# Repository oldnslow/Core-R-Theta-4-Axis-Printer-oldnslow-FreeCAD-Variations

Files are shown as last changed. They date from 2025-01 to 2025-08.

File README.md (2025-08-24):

# The Core R-Theta Printer

This repository is intended to be a series of FreeCAD versions of jyjbird's 4 axis, polar, "core-RΘ" 3D printer – an entirely new type of multi axis 3D printer designed from the ground up. To start a FreeCAD version of the "original" (f8d197c circa 16 Mar 2025 commit) will be generated.  Check out the [Wiki](https://github.com/oldnslow/Core-R-Theta-4-Axis-Printer/wiki) for build guides, links to useful sites/videos and other hopefully useful information. 

Check out jyjbird's [youtube video](https://www.youtube.com/watch?v=VEgwnhLHy3g) to see it in action!
Watch the video (https://www.youtube.com/watch?v=VEgwnhLHy3g)

### Slicer
A multi axis printer is pretty hopeless without a non-planar slicer, which is why I built this quick [radial slicer](https://github.com/jyjblrd/Radial_Non_Planar_Slicer) for the printer. This leverages the printer's rotating nozzle to print simple parts without supports, but there are some limitations to it which I cover in the YouTube video. I'm also working on an optimization based slicer which will be able to print any object without support so stay tuned for that!



### Assembly
There is a wealth of knowledge in the Discussions, Pull Requests and Issues tabs of this repo. The printer is by no means "plug and play", and there are no instructions as of yet, but the information in the discussions should help you get started. Feel free to post questions on the discussions tab.

You can view the [3d model online](https://viewer.autodesk.com/id/dXJuOmFkc2sub2JqZWN0czpvcy5vYmplY3Q6YTM2MHZpZXdlci1wcm90ZWN0ZWQvdDE3NDM1MjM1ODlfN2I3YjNkNzYtYTQ2NC00Y2YzLTgxZDYtYjk0MGJjMjlhMTJmLmYzZA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) to see how to assemble the printer. Everything is 3D printable, however I got the extruder mount made out of metal by JLCPCB as there is quite a bit of torque on that part. I've also included the gerber files to make your own PCB buildplate, but a sheet of MDF wood would also work.

### BOM
Links to Aliexpress stores are included so you know what to get, but they are not neccesarily the best source for your country or build goals.  Click thumbnails to expand. * indicates alternates.
| Component | Qty | Function | Source | Store Search Hint | Image |
| --- | --- | --- | --- | --- | ----- |
| __Frame and Linear Motion__ | | | | |
| 2040 T-Slot Extrusion 350mm | 1 | Frame Vertical | [Aliexpress Magic Dragon](https://www.aliexpress.com/store/911747370) | Select _Products > Aluminum Extrusion_ |  |
| 2040 T-Slot Extrusion 100mm | 1 | Frame Horizontal | [Aliexpress Magic Dragon](https://www.aliexpress.com/store/911747370) | Select _Products > Aluminum Extrusion_ |  |
| 2020 T-Slot Extrusion 150mm | 1 | Frame C Axis | [Aliexpress Magic Dragon](https://www.aliexpress.com/store/911747370) | Select _Products > Aluminum Extrusion_ |  |
| 2020 T-Slot Extrusion 250mm | 1 | X Axis | [Aliexpress Magic Dragon](https://www.aliexpress.com/store/911747370) | Select _Products > Aluminum Extrusion_ |  |
| 2020 T-Slot Corner Bracket | $${\color{red}{\textbf{3?}}}$$ | Frame & C Axis | [Aliexpress Magic Dragon](https://www.aliexpress.com/store/911747370) | Select _Products > Aluminum Extrusion, Corner Bracket_ |  |
| MGN9 250mm Linear Guide __with__ MGN9 __C__ Carriage | 1 | X Axis | [Aliexpress Magic Dragon](https://www.aliexpress.com/store/911747370) |  Select _Products > Linear Guide>MGN9_ |  |
| MGN9 __C__ Carriage | 1 | X Axis additional Linear Carriage | [Aliexpress Magic Dragon](https://www.aliexpress.com/store/911747370) | Select _Products > Linear Guide>MGN9_ |  |
| MGN12 250mm Linear Guide __with__ MGN12 __H__ Carriage | 2 | Z Axis | [Aliexpress Magic Dragon](https://www.aliexpress.com/store/911747370) |Select _Products > Linear Guide>MGN12_ |  |
| | | | | |
| __Drive__ | | | | |
| NEMA 17 External Linear Stepper Motor 40mm with 300 mm T8\*8 Lead Screw | 1 | Z Axis | [Aliexpress JooWo](https://www.aliexpress.com/store/1102798183) | Store Search _Linear Stepper Motor Lead Screw_ |  |
| NEMA 17 External Linear Stepper Motor 40mm with 310 mm T8\*8 Lead Screw | 1\* | Z Axis \*Alternate | [Aliexpress Stepperonline](https://stepperonline.aliexpress.com/store/1984315) | Select Products _Linear_Stepper_ |  |
| T8\*8 Lead Screw Nut H Flange | 1 | Z-Axis | [Aliexpress Kingroon](https://kingroon.vi.aliexpress.com/store/1905393) | Store Search _T8 Nut H Flange_ |  |
| Nema 17 Stepper Motor 34 mm | 3 | XB & C Axes | [Aliexpress Stepperonline](https://stepperonline.aliexpress.com/store/1984315) | Select _Products > Open Loop Motor_ |  |
| GT2 Timing Belt Loop 400mm | 1 | C Axis | [Aliexpress ZHong Trans](https://www.aliexpress.com/store/1103769376) | Select _Products > Timing Belt_ |  |
| GT2 Timing Belt Loop $${\color{red}{\textbf{410mm}}}$$ | 1\* | C Axis \*Alternate | [Aliexpress ZHong Trans](https://www.aliexpress.com/store/1103769376) | Select _Products > Timing Belt_ |  |
| GT2 Timing Belt Loop 752 mm | 1 | XB Axes | [Aliexpress ZHong Trans](https://www.aliexpress.com/store/1103769376) | Select _Products > Timing Belt_ |  |
| GT2 Timing Belt Loop $${\color{red}{\textbf{760 mm}}}$$ | 1\* | XB Axes \*Alternate | [Aliexpress ZHong Trans](https://www.aliexpress.com/store/1103769376) | Select _Products > Timing Belt_ |  |
| GT2 Timing Pulley 40Tooth, __Type AF__ 6 mm Belt, 5 mm Bore &le; 11.3 mm | 1 | B Axis | [Aliexpress ZHong Trans](https://www.aliexpress.com/store/1103769376) | Select _Products > 2GT Pulley_ |  |
| GT2 Timing Pulley 16Tooth, Type KF, 6 mm Belt, 5 mm\* Bore | 3 | XB & C Axes | [Aliexpress ZHong Trans](https://www.aliexpress.com/store/1103769376) | Select _Products > 2GT Pulley_ |  |
| GT2 Timing Pulley 16Tooth, __Type AF__ 6 mm Belt, 5 mm Bore &le; 11.3 mm | $${\color{red}{\textbf{1\*}}}$$ | C Axis \*Alternate to mount bed directly without springs | [Aliexpress Mulge](https://www.aliexpress.com/store/1103508278) | Select _Products > 2GT Pulley_ |  |
| GT2 Idler 16T w/ Teeth, 6 mm Belt, 3 mm Bore | 3 | XB Axes | [Aliexpress ZHong Trans](https://www.aliexpress.com/store/1103769376) | Select _Products > 2GT Pulley_ |  |
| GT2 Idler 16T w/o Teeth, 6 mm Belt, 3 mm Bore | 4 | XB Axes | [Aliexpress ZHong Trans](https://www.aliexpress.com/store/1103769376) | Select _Products > 2GT Pulley_ |  |
| | | | | |
| __Electronics__ | | | |
| The Core-R&theta; printer requires __5 Axes__ and currently its kinematics are only supported by RepRapFirmware (RRF) | | See [Team Gloomy Supported Board List](https://teamgloomy.github.io/supported_boards.html) for lower cost alternates to [Duet 3D control boards](https://www.duet3d.com/) | | |
| Fly E3 Pro Ultra | 1 | 5-Axis RRF Control Board | [Aliexpress Mellow 3D](https://mellow.aliexpress.com/store/1531088) | Select _Products > Fly Electronic Board_ |  |
| Fly Super 5 Pro | 1\* | 5-Axis RRF Control Board \*Alternate | [Aliexpress Mellow 3D](https://mellow.aliexpress.com/store/1531088) | Select _Products > Fly Electronic Board_ |  |
| Duet 3D Mini 5+ | 1\* | 5-Axis RRF Control Board \*Alternate | [Duet 3D](https://www.duet3d.com/) | Select _Products_ |  |
| Micro SD Card &le;32GB, Speed &ge;Class 4 | &ge;1 | [Required for WiFi/headless](https://teamgloomy.github.io/fly_e3_pro_v3_connected_wifi_3_5.html) Team Gloomy recommends 8GB | [Aliexpress MicroStick](https://www.aliexpress.com/store/2393021) | Select _Products > Memory Card > Microdata_ |  |
| 24V 10A Power Brick | 1 | Motion control & air pump | [Aliexpress Shop5496179](https://www.aliexpress.com/store/5496179) | Select _Products > Adapters > AC-DC Adapters_ |  |
| 5.5x2.5 mm Female Jack Panel Mount | 1 | Control board enclosure | [Aliexpress Javino](https://javino.aliexpress.com/store/5258094) | Select _Products > Connector...> DC Plug & Socket_ |  |
| 5.5x2.5 mm Jack Set | 1\* | Control board enclosure \*Alternate for non brick supply | [Aliexpress Javino](https://javino.aliexpress.com/store/5258094) | Select _Products > Connector...> DC Plug & Socket_ |  |
| 18-28 AWG Wire | 1 | General | [Aliexpress Javino](https://javino.aliexpress.com/store/5258094) | Select _Products > Tools..._ |  |
| Limit Switch, Generic | 1 | Bed Z Probe | [Aliexpress Kingroon](https://kingroon.vi.aliexpress.com/store/1905393) | Store Search _Endstop Mechanical Limit Switch_ |  |
| Limit Switch Omron SS-5-2 | 1\* | Bed Z Probe  \*Alterate | Electronics supplier | Store Search _SS-5-2_ |  |
| 4010 24 V Fan | 2 | Control Board Cooling | [Aliexpress STC Cooling](https://www.aliexpress.com/store/1017947) | Select _Products > DC Fan > 40 mm_ |  |
| Quick Connect Set 2.8 4.8 6.3 mm | 1 | Limit switch & misc | [Aliexpress Daevkaema](https://www.aliexpress.com/store/1103885952) | Select _Products > Terminal & Connector_ |  |
| Heat Shrink Tubing Set | 1 | General | [Aliexpress Daevkaema](https://www.aliexpress.com/store/1103885952) | Select _Products > Heat Shrinkable_ |  |
| JST-PH Terminal Crimping Pliers | 1 | Control Board Connections | [Aliexpress IWISS Tools](https://vi.aliexpress.com/store/602708) | Store Search _JST-PH_ |  |
| | | | | |
| __Printing Components__  | | | | |
| BIQU H2 V2S Extruder | 1 | Joy & Anguish | [Aliexpress Big Tree Tech](https://www.aliexpress.com/store/228623) | Select _Products > H2S Extruder..._ |  |
| Airbrush Nozzle Adapter | &ge;1 | Lengthen nozzle reach for non-planar! Spares recommended | [Aliexpress 5A Plus](https://www.aliexpress.com/store/1504095) | Search Store _Airbrush Nozzle Adaptor_ |  |
| Print Bed 250 mm Dia Self Made| 1 | Print Bed | Light, stiff material | 3x3 mm Countersunk holes on 150 mm dia circle |  |
| Print Bed 250 mm Dia | 1\* | Aluminum Print Bed \*Alternate | $${\color{red}{\textbf{[JLCCNC or JLCCNC}}}]$$(https://jlccnc.com/) | $${\color{red}{\textbf{Step File?}}}$$ |  |
| Print Bed 250 mm Dia | 1\* | PCB Print Bed \*Alternate | [JLCPCB](https://jlcpcb.com/) | _pcb buildplate_ |  |
| Print Bed ~ $${\color{red}{\textbf{??mm Dia}}}$$ | 1\* | Print Bed \*Alternate | $${\color{red}{\textbf{Aliexpress or other?}}}$$ |  |  |
| Micro Vacuum Pump __24V__ | 1 | Part cooling | [Aliexpress Hua02](https://vi.aliexpress.com/store/1103052669) | Search Store _Micro Vacuum Pump_ |  |
| Silicone Tubing 6 mm ID x 8 mm OD | 1-5 m | Part Cooling | [Aliexpress First Met](https://www.aliexpress.com/store/1102770486) | Store Search _Silicone Hose_ |  |
| Filament Spool Holder | 1 |  | [Aliexpress 5A Plus](https://www.aliexpress.com/store/1504095) | Search Store _Filament Spool Holder_ |  |
| PTFE Tube 2 mm ID x 8 mm OD | 1 |  | [Aliexpress 5A Plus](https://www.aliexpress.com/store/1504095) | Select _Products > Teflon Tube_ |  |
| | | | | | 
| __Hardware__ | | | | |
| 2020 T-Slot Sliding Nut M4 | 50 | Frame | [Aliexpress Magic Dragon](https://www.aliexpress.com/store/911747370) | Store Search _Sliding Nut_ |  |
| 2020 T-Slot Sliding Nut M3 | 50 | Linear Guides | [Aliexpress Magic Dragon](https://www.aliexpress.com/store/911747370) | Store Search _Sliding Nut_ |  | 
| M4 Screw Set | 1 | Frame | [Aliexpress Wzhuida](https://wzhuida.aliexpress.com/store/1102997921) | Store Search _M4 Metric Screw Assortment Hex Socket Head Cap_ |  | 
| M3 Socket Head Cap Screw Set, __include 40 mm__ | 1 | Linear Guides & General | [Aliexpress Wzhuida](https://wzhuida.aliexpress.com/store/1102997921) | Store Search _M3 Screw Assortment, M3x6-50mm_ |  |
| M3 Flat Head Screw DIN7991, __include 2x20 mm, 3x25 mm__ | 1 | Extruder & Bed Mounts | [Aliexpress Wzhuida](https://wzhuida.aliexpress.com/store/1102997921) | Store Search _Flat Head Screw_ |  |
| M3 Square Nut DIN562 | 50 | General | [Aliexpress Liya Hardware](https://aiscrew.aliexpress.com/store/1960312) | Store Search _DIN562 Thin Nut_ |  |
| M3 Hex Nut DIN985 | 5 | Bed Mount & C Axis Tension | [Aliexpress Wzhuida](https://wzhuida.aliexpress.com/store/1102997921) | Store Search _DIN985_ |  |
| 5x20x0.5-1.0 mm Compression Spring | 3 | Bed Mount | [Aliexpress Zrui](https://www.aliexpress.com/store/1102733418) | Store Search _Micro Small Compression Spring_ |  |
| MR85ZZ 5x8x2.5 mm Bearing | 4 | B axis | [Aliexpress Magic Dragon](https://www.aliexpress.com/store/911747370) | Store Search _MR85ZZ_ |  |
| MR85ZZ 5x8x2.5 mm ABEC-9 Bearing | 4\* | B axis \*Alternate | [Aliexpress APE Official](https://www.aliexpress.com/store/1103773651) | Store Search _MR85ZZ_ |  |
| 6810ZZ 50x65x7 mm Bearing | 2 | C axis | [Aliexpress Kandle](https://kandebearingsshop.aliexpress.com/store/3862082) | Search Store _6810ZZ_ |  |
| 6810ZZ 50x65x7 mm ABEC-9 Bearing | 2\* | C axis \*Alternate | [Aliexpress Shop1104...](https://www.aliexpress.com/store/1104628632) | Search Store _6810ZZ_ |  |
| 5x50 mm Cylindrical Pin or Rod | 1 | B axis shaft | [Aliexpress YMAX](https://www.aliexpress.com/store/912228060) | Search Store _Cylindrical Pins for DIY_ |  | 
| 5x11x6 mm Shaft Collar| 1 | B axis | [Aliexpress JZN](https://jznb.aliexpress.com/store/3204060) | Store Search _SCCAW_ |  |
| 12x8x9H x 3D  mm Rubber Foot| 1 | Frame | [Aliexpress TonKing](https://tonking.aliexpress.com/store/1709973) | Store Search _Small Shock_ |  |
| 17x13x14H x 3D  mm Rubber Foot| 3 | Frame | [Aliexpress TonKing](https://tonking.aliexpress.com/store/1709973) | Store Search _Small Shock_ |  |

Bibtex Citation:
```
@software{Bird_Core_R-Theta_Printer,
author = {Bird, Joshua},
license = {View repository for custom license.},
title = {{Core R-Theta Printer}},
url = {https://github.com/jyjblrd/Core-R-Theta-4-Axis-Printer}
}
```

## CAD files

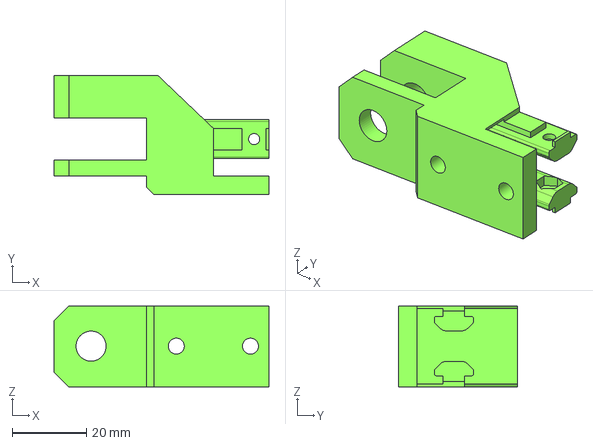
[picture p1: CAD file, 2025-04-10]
Core-R-Theta Std 20250316 Measure.step
58.0 x 32.2 x 21.8 mm

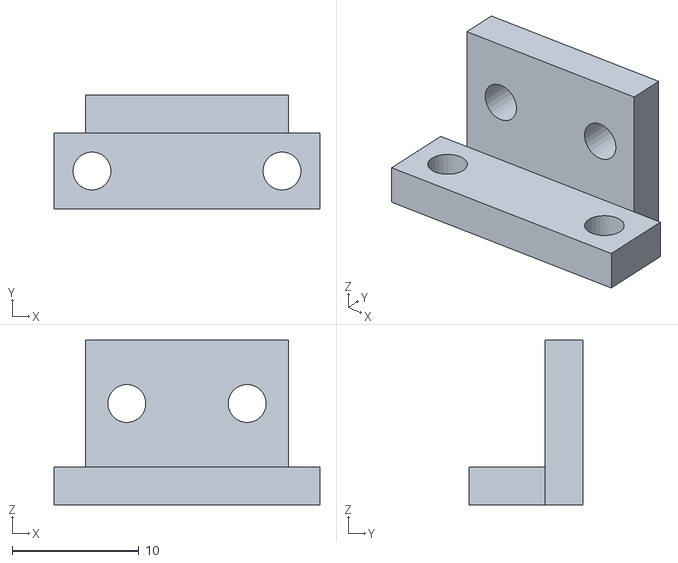
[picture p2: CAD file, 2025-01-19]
stl files/z probe bracket.stl
21.0 x 9.00 x 13.0

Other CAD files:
4 axis polar 3d printer Fusion360 .f3d files/0616e7d9-f380-47b4-a429-0148fa68df5b.f3d
4 axis polar 3d printer Fusion360 .f3d files/79d08786-4967-4a0b-b894-2fc37a93b006.f3d
4 axis polar 3d printer Fusion360 .f3d files/c1aca14e-4cec-4004-bebc-09b1d7cd0bb8.f3d
Core-R-Theta Std 20250316 Measure.FCStd

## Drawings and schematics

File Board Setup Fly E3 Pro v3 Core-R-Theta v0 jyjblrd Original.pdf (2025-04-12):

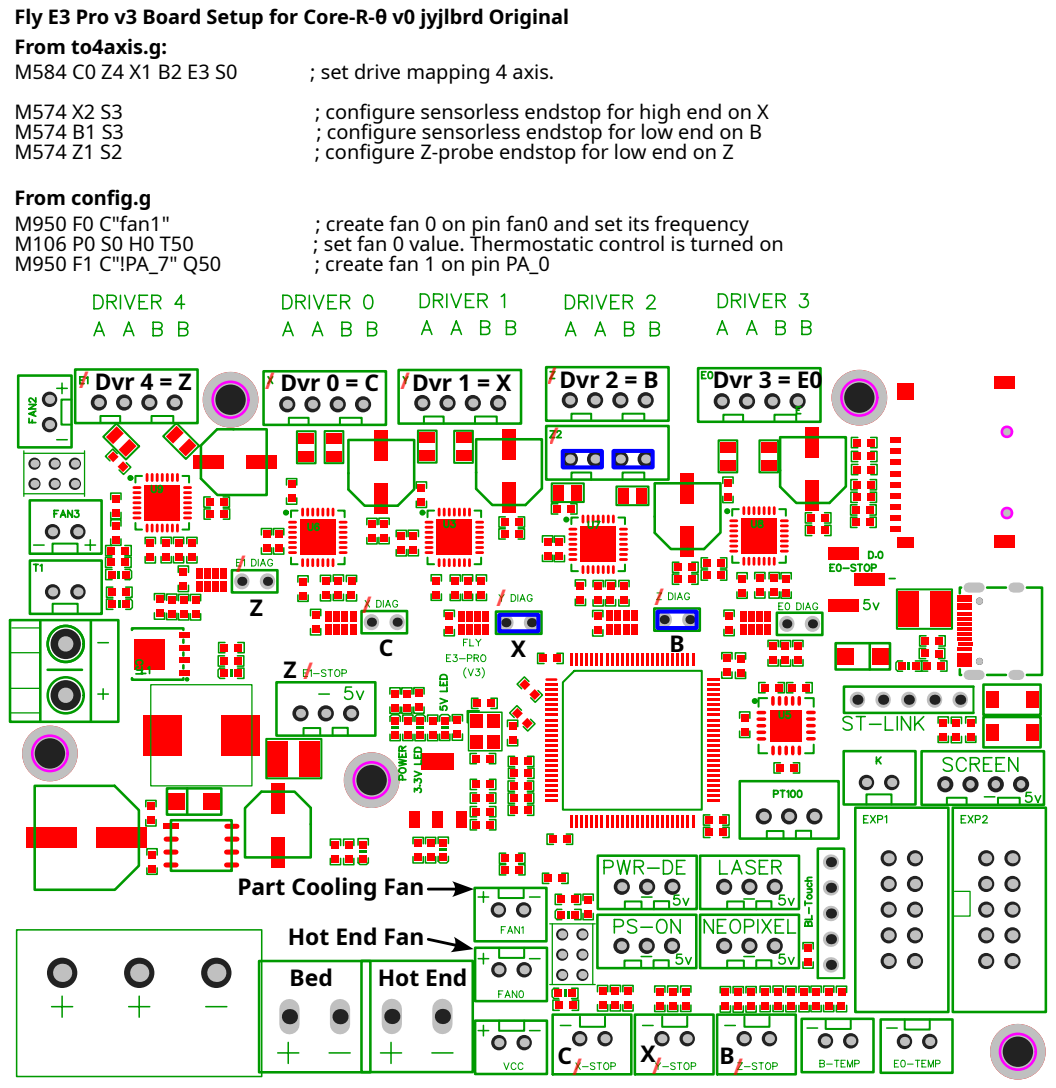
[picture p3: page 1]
Dvr 4 = Z; Dvr 0 = C Dvr 1 = X; Dvr 2 = B; Dvr 3 = E0; ; set drive mapping 4 axis.; ; configure sensorless endstop for high end on X; ; configure sensorless endstop for low end on B; ; configure Z-probe endstop for low end on Z; M950 F0 C"fan1"; ; create fan 0 on pin fan0 and set its frequency; ; set fan 0 value. Thermostatic control is turned on; ; create fan 1 on pin PA_0

Fly E3 Pro v3 Board Setup for Core-R-θ v0 jyjlbrd Original
From to4axis.g:
From config.g

Part Cooling Fan
Hot End Fan
Hot EndBed

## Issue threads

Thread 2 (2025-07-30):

Crossref Some prints have issues with screws

EmmanuelMess, 2025-07-30:
See https://github.com/jyjblrd/Core-R-Theta-4-Axis-Printer/issues/55

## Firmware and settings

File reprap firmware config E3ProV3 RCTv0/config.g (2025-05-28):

; Configuration file for Fly-E3-Pro-v3 (firmware version 3.5)
; executed by the firmware on start-up
;
; generated by RepRapFirmware Configuration Tool v3.5.0-STM32+1 on Sat Aug 03 2024 22:26:49 GMT+0800 (Hong Kong Standard Time)
; Updated 2025 04 26 commit c3e7d44

global B_OFFSET = 0
global X_LENGTH = 115.5                                    ; actually 117.0 but this stops some squshing issues
; global X_LENGTH = 117

; General preferences
G90                                                        ; send absolute coordinates...
M83                                                        ; ...but relative extruder moves
M550 P"Core-R-Theta"                                    ; set printer name

; Network
;M552 S1                                                    ; enable network
M552 S0                                                    ; temporarily disable network to facillitate initial firmaware install

M586 P0 S1                                                 ; enable HTTP
M586 P1 S0                                                 ; disable FTP
M586 P2 S0                                                 ; disable Telnet

; Drives
M84 S30                                                    ; Set idle timeout

; Custom commands for 4 axis / polar configuration
; M98 P"to4axis.g"
M98 P"topolar.g"

; sensorless endstop configuration
M915 B R0 F0 S-10                                                     
M915 X H100 R0 F0 S0                                                     

; Accelerometer
;M955 P0 C"PB_2+PA_10" I46                                 ; disable as not used by Core-R-Theta

; Input shaping
; M593 P"zvddd" F38

; Z-Probe
M558 P5 C"^xstop" H5 F2000:500 T6000 A1                    ; set Z probe type to switch and the dive height + speeds
G31 P500 X0 Y0 Z-8.5                                       ; set Z probe trigger value, offset and trigger height

; Heaters
M140 H-1                                                   ; disable heated bed (overrides default heater mapping)
M308 S0 P"e0temp" Y"thermistor" T100000 B4956 C1.587780e-7 ; configure sensor 0 as thermistor on pin e0temp
M950 H0 C"e0heat" T0                                       ; create nozzle heater output on e0heat and map it to sensor 0
M307 H0 R2.703 K0.364:0.000 D11.05 E1.35 S1.00 B0 V23.7    ; pwm config from autotune
M143 H0 S270                                               ; set temperature limit for heater 0 to 120C
M302 P1                                                    ; allow cold extrudes

; Fans
M950 F0 C"fan1"                                            ; create fan 0 on pin fan0 and set its frequency
M106 P0 S0 H0 T50                                          ; set fan 0 value. Thermostatic control is turned on

M950 F1 C"!PA_7" Q50                                       ; create fan 1 on pin PA_0

; Tools
M563 P0 D0 F0 H0                                           ; define tool 0
G10 P0 X0 Y0 Z0                                            ; set tool 0 axis offsets
G10 P0 R0 S0                                               ; set initial tool 0 active and standby temperatures to 0C
T0                                                         ; select tool

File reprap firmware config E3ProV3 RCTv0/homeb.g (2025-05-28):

M400                  ; Wait for current moves to finish
M913 X50 B50          ; drop motor current
M569 P1 V1            ; put driver 1 into stealth chop mode
M569 P2 V1            ; put driver 2 into stealth chop mode
M400
G91                   ; relative positioning
; G1 H2 Z10 F12000   ; lift Z relative to current position
G1 H2 X-10 B-10 F1000 ; go back a few mm
G1 H1 B1000 F200000   ; move quickly to X axis endstop and stop there (first pass)
G1 H0 B-90 F12000      ; go back a few mm
G1 H1 B1000 F200000   ; move slowly to X axis endstop once more (second pass)
; G1 H2 Z-10 F6000   ; lower Z again
G90                   ; absolute positioning
M400
M913 X100 B100        ; return current to 100%
M569 P1 V4000         ; put driver 1 into spread cycle mode
M569 P2 V4000         ; put driver 2 into spread cycle mode
M400
G1 B0 F12000

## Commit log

2025-04-01 Add files via upload
    Fussion360.f3d files extracted from .f3z file for easy access for non Fusion360 users
    [0616e7d9-f380-47b4-a429-0148fa68df5b.f3d, 79d08786-4967-4a0b-b894-2fc37a93b006.f3d, c1aca14e-4cec-4004-bebc-09b1d7cd0bb8.f3d]
2025-04-02 Update README.md
    Specify control board, add line for micro sd card, point to aliexpress stores for a hopefully more persistent link
2025-04-04 Update README.md
    add dimensions to C axis bearing bom
2025-04-10 FreeCAD from Step and Coloured Step file
    [Core-R-Theta Std 20250316 Measure.FCStd, Core-R-Theta Std 20250316 Measure.step]
2025-04-12 Board jumper set up pdf
2025-04-13 Rename reprap directory
    [config.g]
2025-04-14 add original config
    [config.g, homeall.g, homeb.g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]
2025-04-17 disable network and accelerometer
    [config.g]
2025-05-28 Update with jyjbird commit c3e7d44
    [config.g, homeall.g, homeb.g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]
2025-05-28 Modified jyjblrd commit c3e7d44
    Accelerometer disabled, network disabled to facilitate initial control board firmware update
    [config.g, homeall.g, homeb.g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]
2025-08-24 Update BOM to remove optional B Axis Coupling
